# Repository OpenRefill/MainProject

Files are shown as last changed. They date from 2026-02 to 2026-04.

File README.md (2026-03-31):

# OpenRefill 
An open-source platform for refill and reuse dispenser systems. 

## The Mission
We want to accelerate the shift away from single-use plastic by enabling open, low-cost refill dispensing systems, through open-source designs, shared standards, and collaboration. Our focus is on personal care products (shampoos, conditioners, soaps, etc) that are sold to developing markets in sachets. 

Find out more at [openrefill.com](https://openrefill.com) and dive deeper at our [research wiki](https://github.com/OpenRefill/OpenRefill/wiki/Research). 

## Getting started
1. Read the [licence notice](LICENCE-NOTICE.md) and understand your freedoms and responsibilities.
2. Read our [code of conduct](CODE_OF_CONDUCT.md) and our [contribution guidelines](CONTRIBUTING.md).
3. Check out our [discussions page](https://github.com/OpenRefill/OpenRefill/discussions). Feel free to introduce yourself in [Welcome to OpenRefill Discussions!](https://github.com/OpenRefill/OpenRefill/discussions/1#discussion-9450050).
4. Review our [open issues](https://github.com/OpenRefill/MainProject/issues) to start contributing.
5. Understand the logistics, operational, and business model dimensions of deploying a refill service by heading to [Refill Realities](https://www.refillrealities.com/#playbooks) and reading their playbooks. 

## Need help? 
- Email us at hello@openrefill.com.

## Follow Us 
[LinkedIn](https://www.linkedin.com/company/open-refill/?viewAsMember=true) 
#openrefill 
#refillrevolution

## Original Contributors

OpenRefill is a collaborative effort brought to life by industry leaders in smart logistics, digital innovation, and global sustainability:

* **[Smartfill](https://smartfill.store)** – A leading global supplier of smart dispensers and cloud-based logistics and inventory management for bulk products.
* **[DY|DX Digital](https://dydx.digital)** – A leading innovation consultancy.
* **[TRANSFORM](https://www.transform.global/home.html)** – A joint initiative between Unilever, the UK Foreign, Commonwealth & Development Office (FCDO), and EY.
* **[BOPINC](https://bopinc.org)** & **[Unilever Bangladesh](https://www.unilever.com.bd/)** – Strategic partners whose work on the **URefill** project provided foundational results for this initiative.

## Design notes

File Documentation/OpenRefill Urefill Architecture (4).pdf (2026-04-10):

# OpenRefill Technical Architecture:

## Urefill Version

2026/03/03

# Overview

The U-Refill cabinet contains 4 liquid personal care dispensers. Each dispenser has the following main components:
- 1x Peristaltic pump
- 1x LCD screen
- 4x Buttons
- 1x Trigger nozzle
- 1x Loadcell
- 1x Peripheral PCB

All the components are attached to the main cabinet, which consists of laser cut and bent metal parts. Some 3d-printed parts are also used, e.g., the button covers.

The dispenser functions as follows:
1. User selects an amount
2. User presses trigger button/nozzle upwards
3. The pump runs for a calibrated time period for the selected volume
4. A receipt is printed out.
5. The dispense event is sent to the cloud interface.

The dispenser load cell weighs the dispenser hopper (5L bottle or jerry can). The loadcell reading can be used to determine if the hopper is empty. Currently though the loadcell implementation is not functional and needs to be redesigned.

### Version History

This document pertains to the U-refill project version. A minor upgrade was manually made to improve the flow rate in 2024. Also an alternative and improved hopper bracket was designed, however not implemented during this time. The main PCB was also updated to include a ground plane. Previously it only had ground traces.

# Mechanical Components

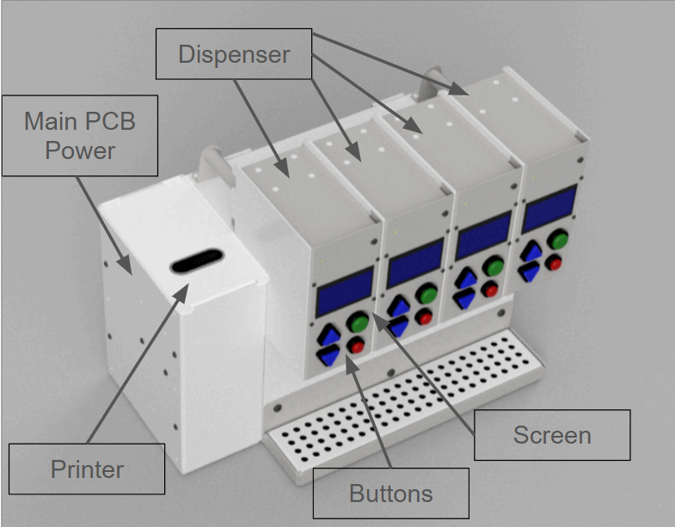
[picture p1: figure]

The cabinet has four dispensers, with a shared power supply, main PCB and printer.

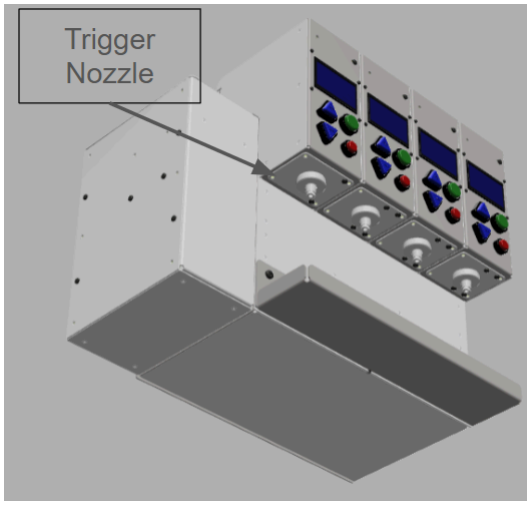
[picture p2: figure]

The trigger nozzle - this is pressed up to start dispensing after selecting an amount.

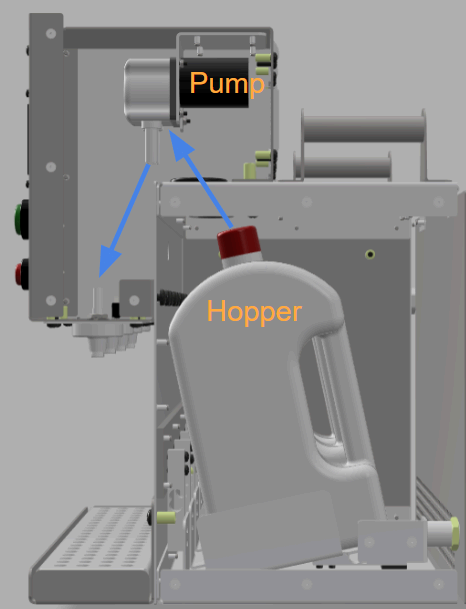
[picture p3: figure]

Side view of a dispenser. The hopper (5L jerrycan or bottle), contains the product supply. The motor pumps the liquid through the tube (blue arrows) to the Trigger Nozzle. Note this shows the updated design for the corrected load cell orientation.

# Electronics

The main PCB controls all four dispensers. The PCB has three ESP32 development boards. The boards communicate with each other using I2C.

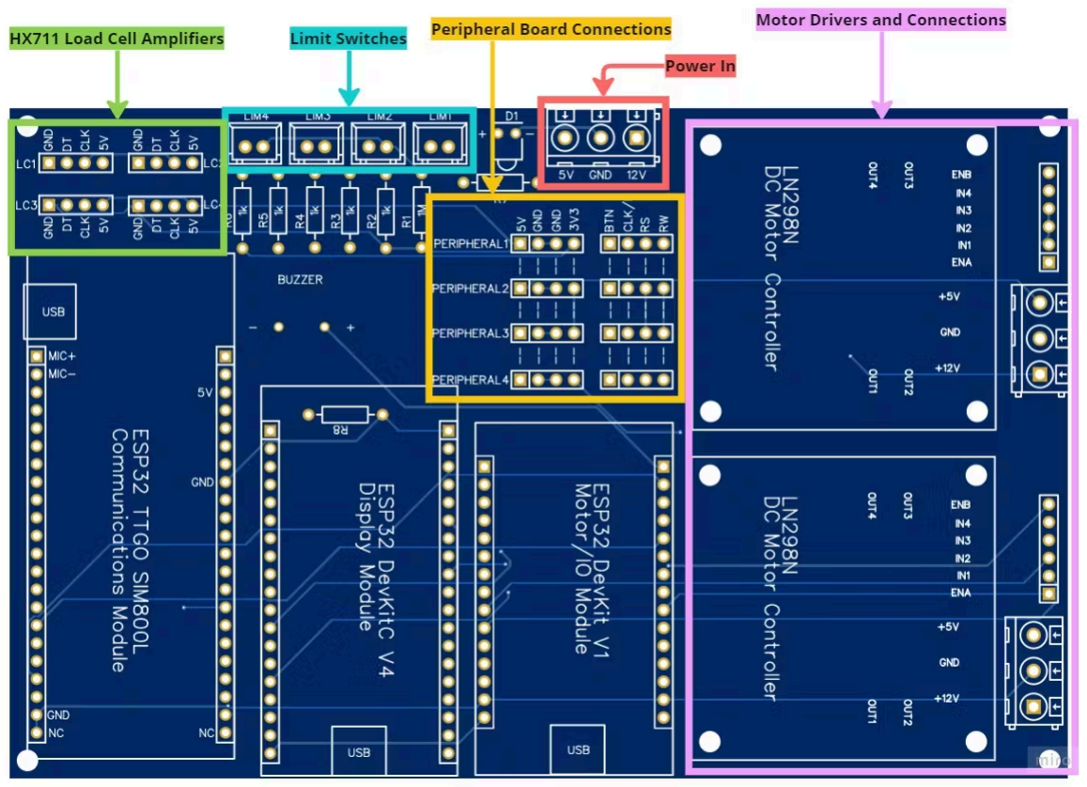
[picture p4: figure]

The main PCB with connection headers.

### Comms Module

Development Board: LILYGO TTGO T-Call V1.4 CH9102F QFN24 ESP32 Wireless Module GPRS Antenna SIM Card SIM800L Board

This ESP communicates with Azure-IoT-Central. The sim-card module mounted on it however does not work with the IoT/ESP internet library, and is not used. A WiFi router is used instead. Internet connection is used to send status updates and dispense events (records) to the cloud database. The current time is also obtained with NTP sync.

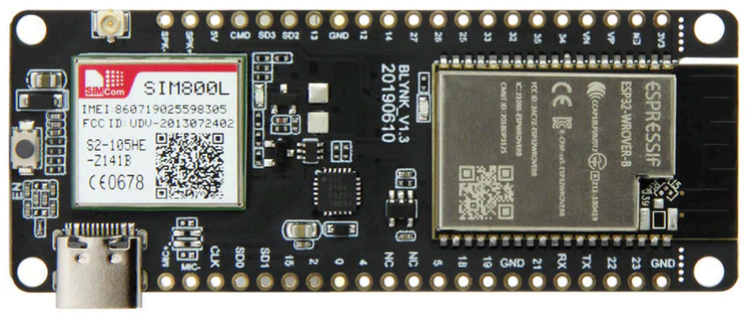
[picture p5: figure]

The LilyGo ESP module with SIM card slot

The loadcell ADC boards are also connected to this ESP. But as noted, the load cell circuit and mechanical orientation are not functional. The HX711 module (breakout board) is used to convert the load cell signal into a digital value using an ADC. The ADC digital output might need to be level shifted (5V to 3.3V).

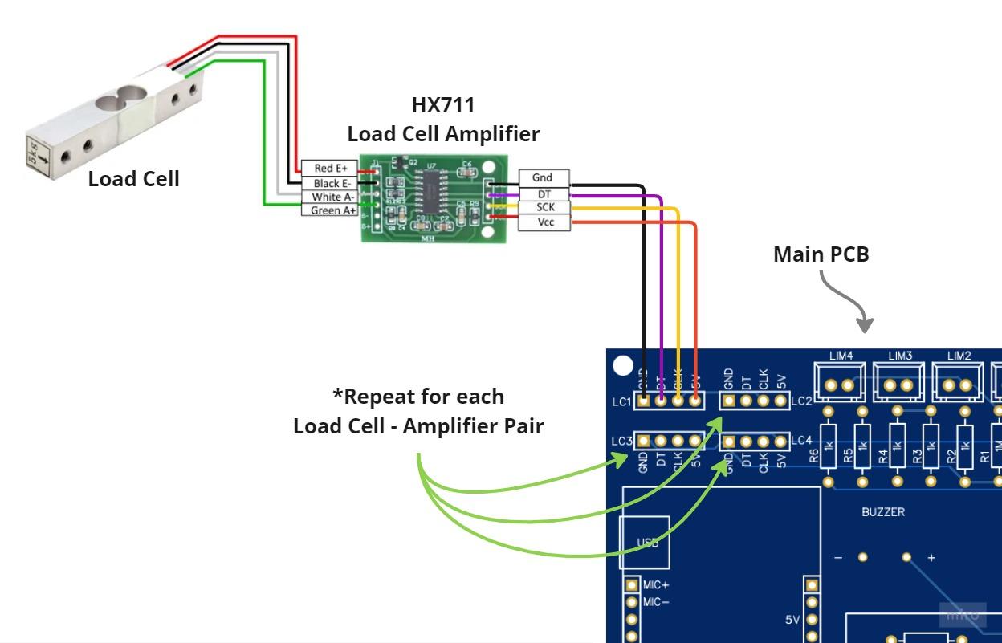
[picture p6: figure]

The loadcell connected to an HX711 loadcell ADC and amplifier, which is connected to the main PCB

### Display Module

Development Board: ESP32-WROOM32 DevKitC V4

This ESP drives all the displays. The display is a 128x64 LCD character display . Currently, the display is set to use only Bangladeshi characters.

The display module connects to each display with the Peripheral PCB.

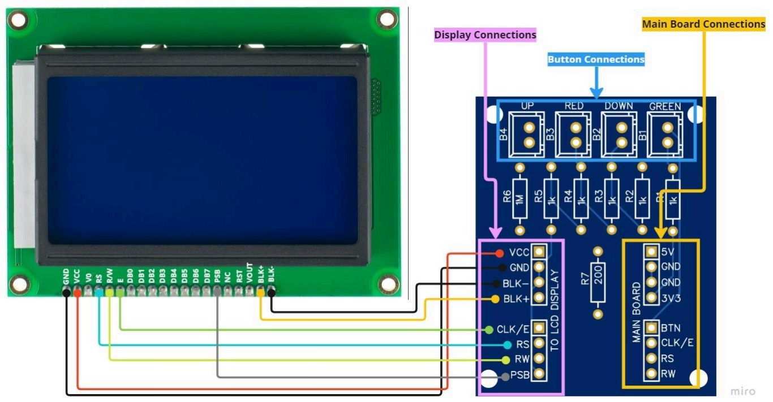
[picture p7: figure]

The display module connected to the peripheral PCB

### Main (Motor and IO) Module

Development Board: ESP32-WROOM32 DEVKIT V1

The main board does the following:
- Controls the four pump motors with DC motor drivers (also breakout boards).
- Check the buttons and trigger status of each dispenser. A resistor ladder is used to reduce the number of input pins required. All the buttons for one dispenser are connected to one pin. The voltage level as read with the ADC is used to determine if a specific button is pressed or not. The four nozzle-trigger buttons are also joined together using the same technique. The buttons are wired via the peripheral PCB to the main PCB.
- Control the buzzer.
- Connects to the Bluetooth printer to print receipts.

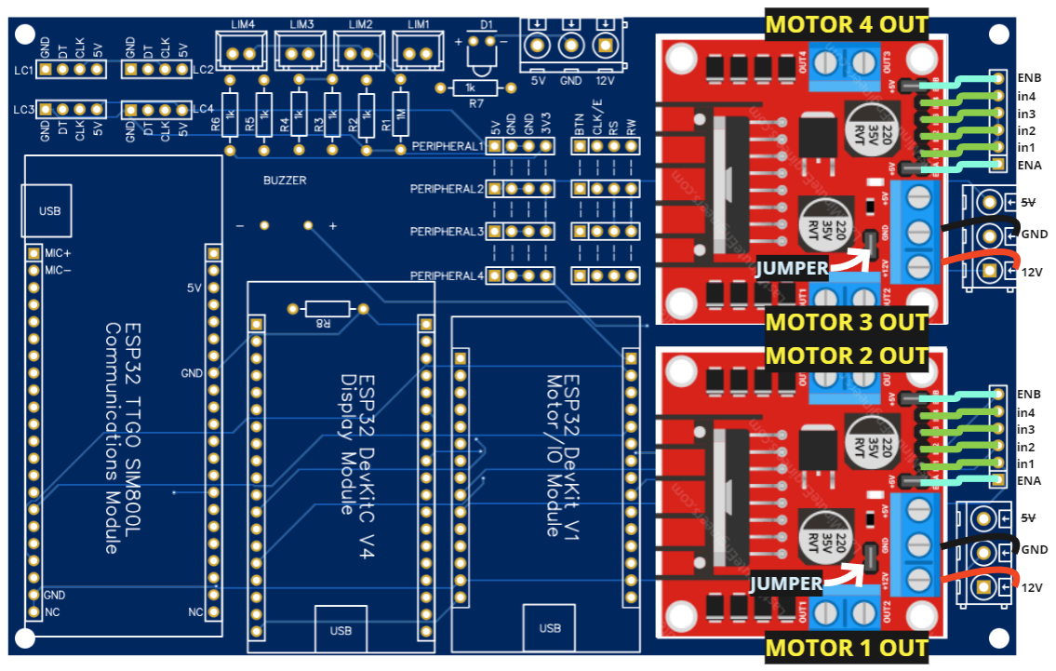
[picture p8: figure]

View of motor drivers mounted on the main PCB

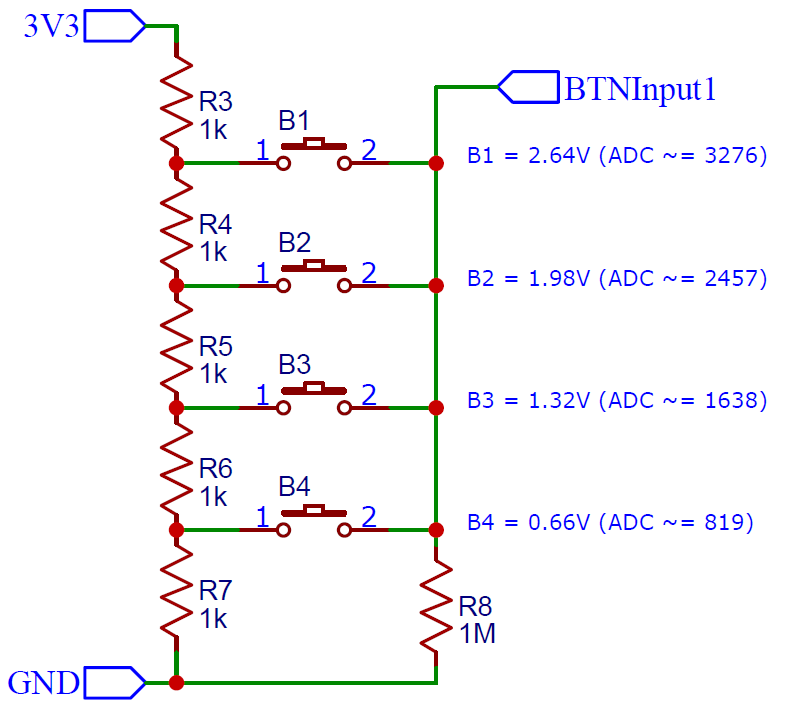
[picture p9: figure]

Voltage ladder used for buttons

### Pin Assignments: Peripheral PCB to Main Board

Pin Name | Pin Type | Description | Notes
5V | Power | 5V Power in
GND | Ground | Signal ground
3V3 | Analog Input | 3.3V reference for button circuit
BTN | Analog Output | Analog button voltage out
CLK/E | Serial Clock | Display clock
RS | Serial Data | Display chip select
R/W | Serial Data | Display data

### Pin Assignments: Peripheral to Display

Pin Name | Pin Type | Description | Notes
VCC | Power | 5V Power
GND | Ground | Signal ground
BLK- | Ground | Backlight cathode (-)
BLK+ | Power | Backlight anode (+)
CLK/E | Serial Clock | Display clock

RS | Serial Data | Display chip select
R/W | Serial Data | Display data
PSB | Digital Input | Parallel/Serial Bit (0=Serial)

## Power Supply

A 12V 10A (120W) power supply with battery connection is used to power the cabinet. A buck converter outputs the 5V power rail, which supplies the screens and ESP boards.

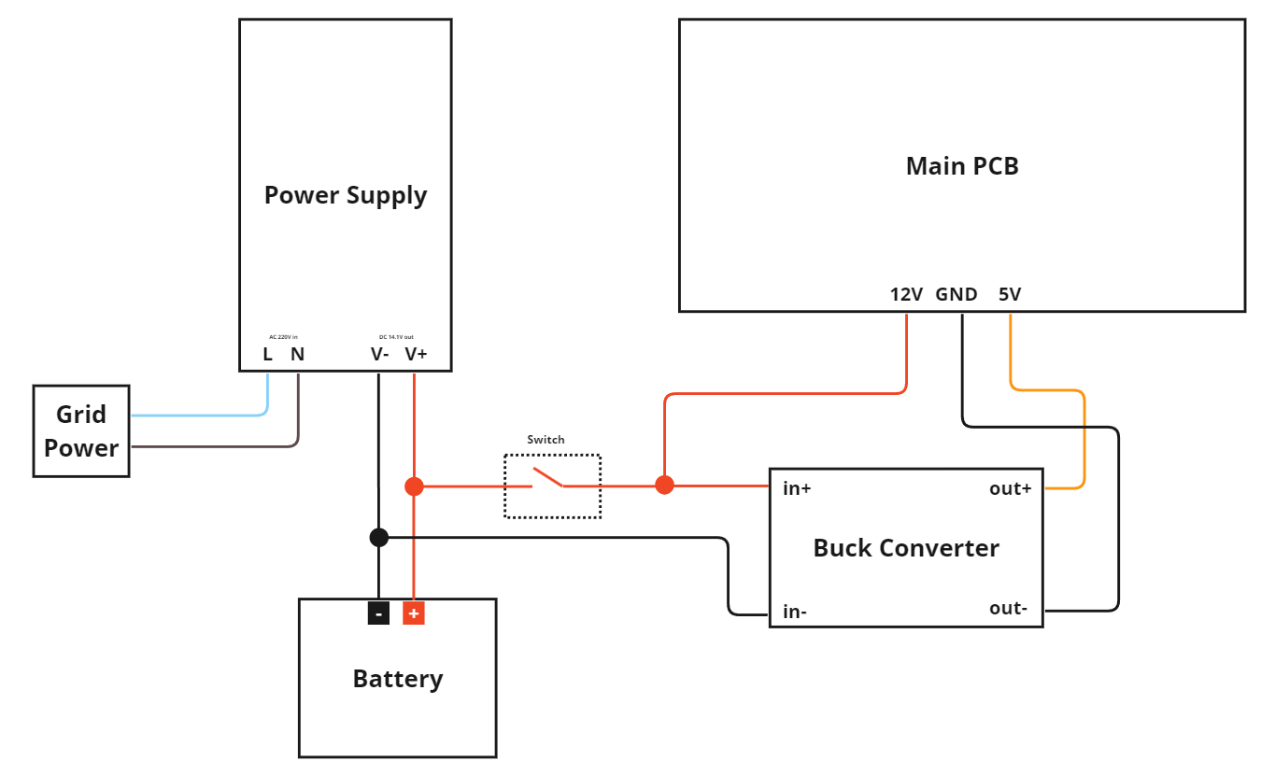
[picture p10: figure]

Block diagram of the power supply

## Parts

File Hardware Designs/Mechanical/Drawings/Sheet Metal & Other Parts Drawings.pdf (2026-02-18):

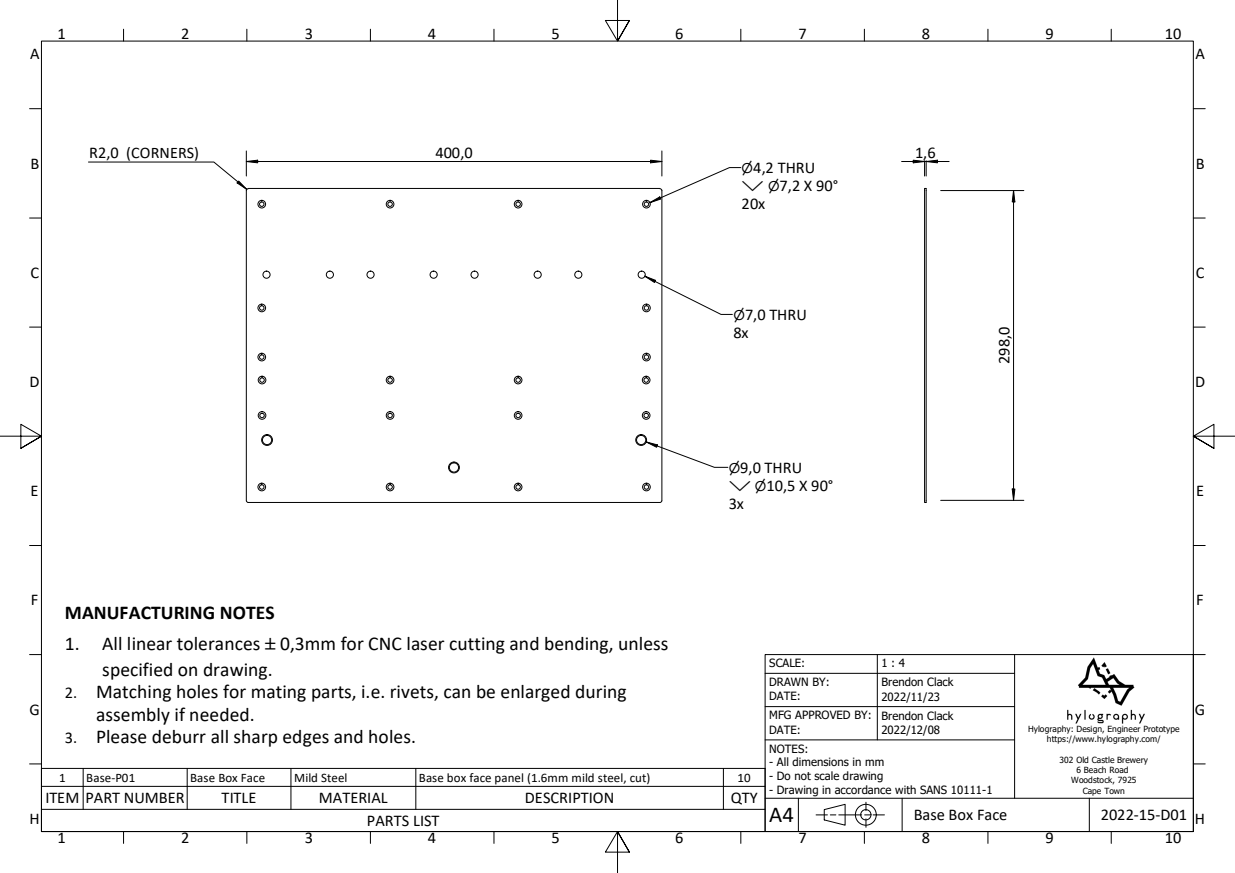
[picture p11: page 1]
PARTS LIST; Base Box Face; ⌀4,2 THRU ⌵ ⌀7,2 X 90°; ⌀7,0 THRU; ⌀9,0 THRU ⌵ ⌀10,5 X 90°; R2,0 (CORNERS)

MANUFACTURING NOTES
1. All linear tolerances `0,3mm for CNC laser cutting and bending, unless
specified on drawing.
2. Matching holes for mating parts, i.e. rivets, can be enlarged during
3. Please deburr all sharp edges and holes.

DRAWN BY: DATE: | Brendon Clack 2022/11/23

assembly if needed.

MFG APPROVED BY: DATE: | Brendon Clack 2022/12/08

Hylography: Design, Engineer Prototype
https://www.hylography.com/

NOTES:
- All dimensions in mm
- Do not scale drawing
- Drawing in accordance with SANS 10111-1

302 Old Castle Brewery
6 Beach Road
Woodstock, 7925
Cape Town

1 | Base-P01 | Base Box Face | Mild Steel | Base box face panel (1.6mm mild steel, cut) | 10
ITEM | PART NUMBER | TITLE | MATERIAL | DESCRIPTION | QTY

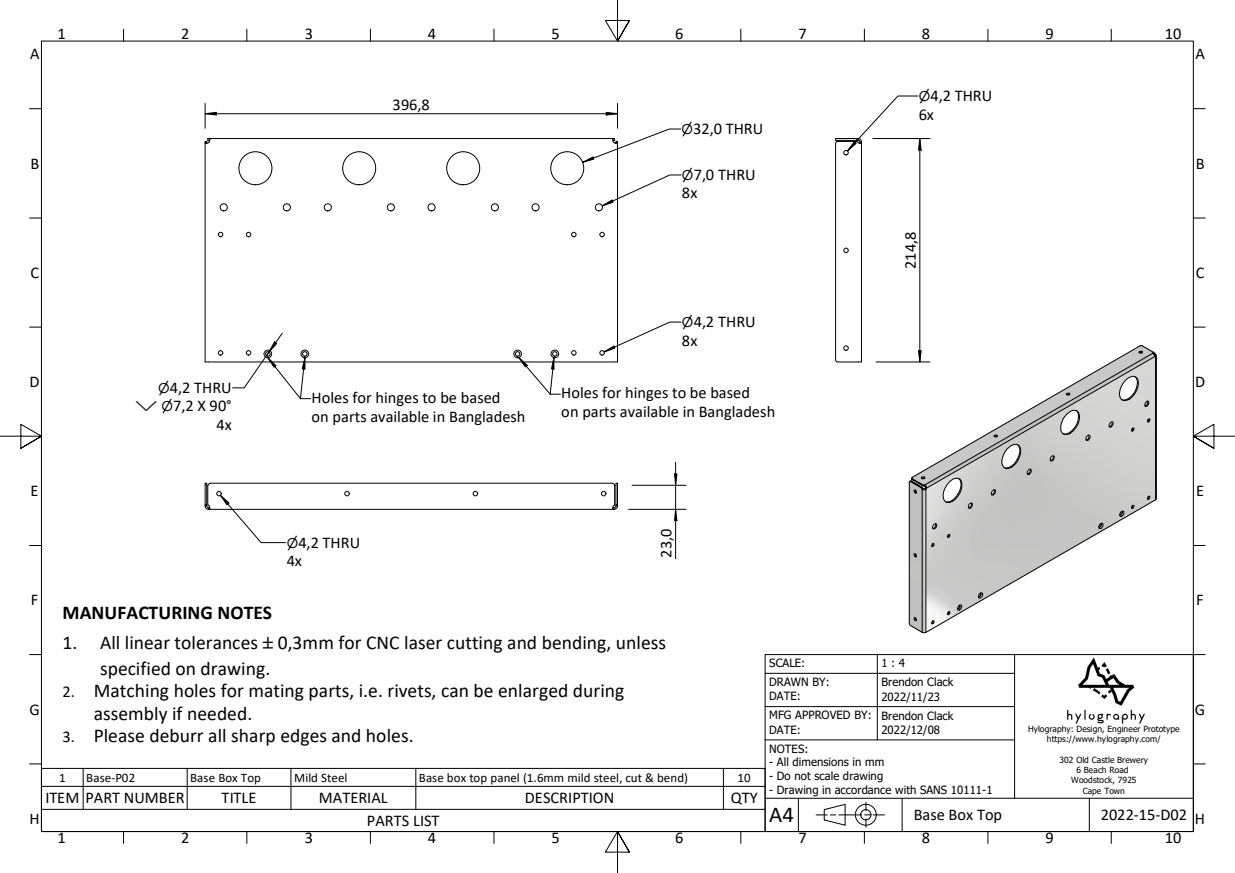
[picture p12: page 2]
Base Box Top; ⌀32,0 THRU; ⌀7,0 THRU; ⌀4,2 THRU ⌵ ⌀7,2 X 90°; ⌀4,2 THRU

Holes for hinges to be based
on parts available in Bangladesh

MANUFACTURING NOTES
1. All linear tolerances `0,3mm for CNC laser cutting and bending, unless
specified on drawing.
2. Matching holes for mating parts, i.e. rivets, can be enlarged during
3. Please deburr all sharp edges and holes.

DRAWN BY: DATE: | Brendon Clack 2022/11/23

assembly if needed.

MFG APPROVED BY: DATE: | Brendon Clack 2022/12/08

Hylography: Design, Engineer Prototype
https://www.hylography.com/

NOTES:
- All dimensions in mm
- Do not scale drawing
- Drawing in accordance with SANS 10111-1

302 Old Castle Brewery
6 Beach Road
Woodstock, 7925
Cape Town

1 | Base-P02 | Base Box Top | Mild Steel | Base box top panel (1.6mm mild steel, cut & bend) | 10
ITEM | PART NUMBER | TITLE | MATERIAL | DESCRIPTION | QTY

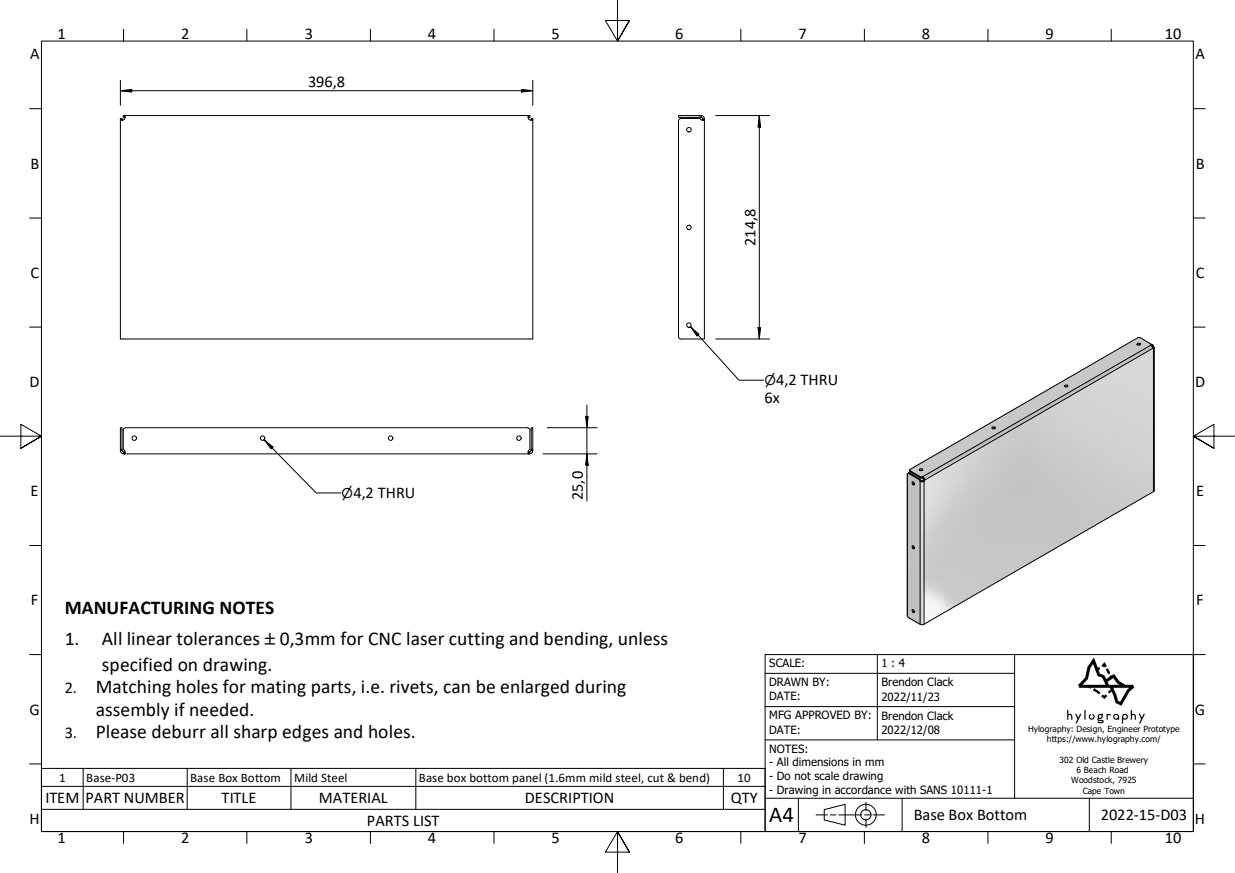
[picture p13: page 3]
Base Box Bottom; ⌀4,2 THRU

MANUFACTURING NOTES
1. All linear tolerances `0,3mm for CNC laser cutting and bending, unless
specified on drawing.
2. Matching holes for mating parts, i.e. rivets, can be enlarged during
assembly if needed.
3. Please deburr all sharp edges and holes.

DRAWN BY: DATE: | Brendon Clack 2022/11/23

MFG APPROVED BY: DATE: | Brendon Clack 2022/12/08

Hylography: Design, Engineer Prototype
https://www.hylography.com/

NOTES:
- All dimensions in mm
- Do not scale drawing
- Drawing in accordance with SANS 10111-1

302 Old Castle Brewery
6 Beach Road
Woodstock, 7925
Cape Town

1 | Base-P03 | Base Box Bottom | Mild Steel | Base box bottom panel (1.6mm mild steel, cut & bend) | 10
ITEM | PART NUMBER | TITLE | MATERIAL | DESCRIPTION | QTY

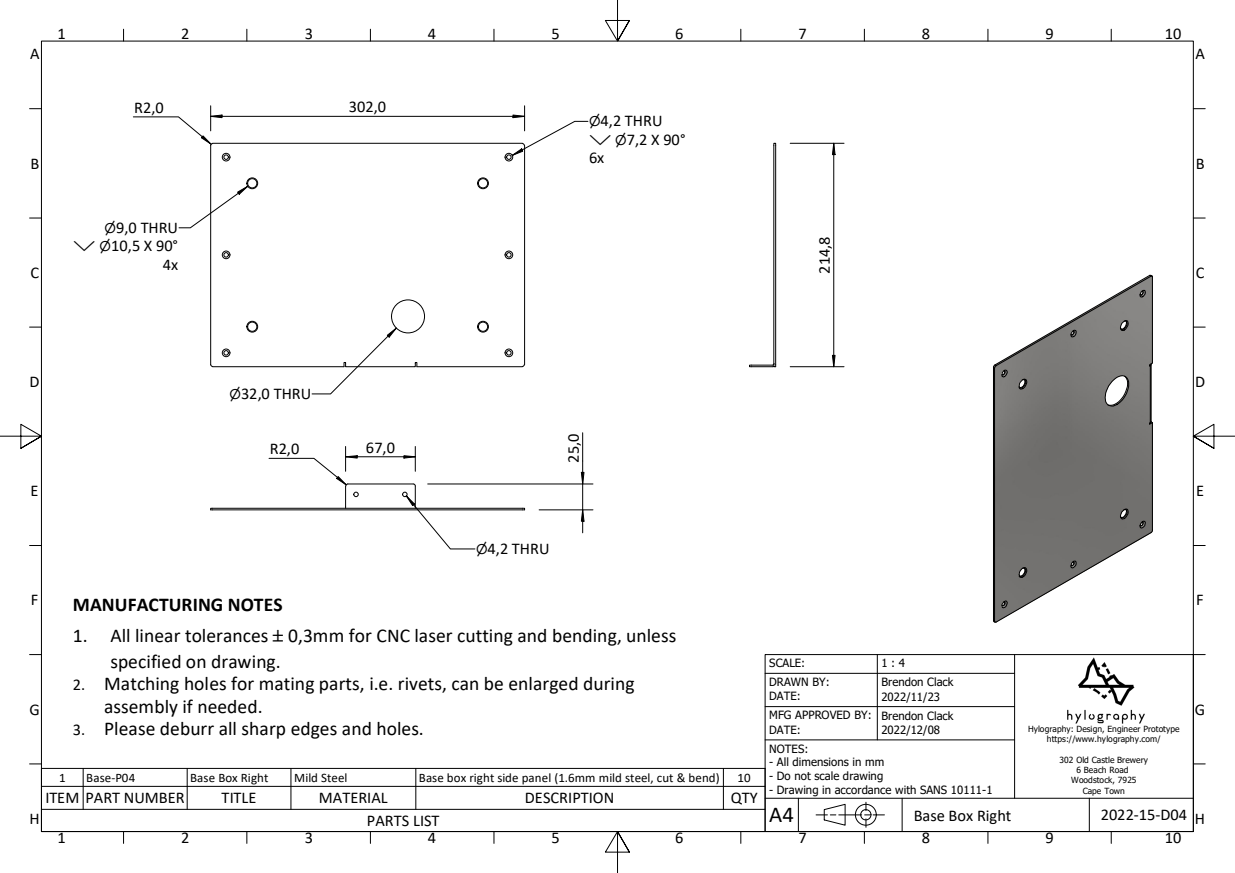
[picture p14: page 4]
Base Box Right; ⌀4,2 THRU ⌵ ⌀7,2 X 90°; ⌀32,0 THRU; ⌀4,2 THRU; ⌀9,0 THRU ⌵ ⌀10,5 X 90°

MANUFACTURING NOTES
1. All linear tolerances `0,3mm for CNC laser cutting and bending, unless
specified on drawing.
2. Matching holes for mating parts, i.e. rivets, can be enlarged during
assembly if needed.
3. Please deburr all sharp edges and holes.

DRAWN BY: DATE: | Brendon Clack 2022/11/23

MFG APPROVED BY: DATE: | Brendon Clack 2022/12/08

Hylography: Design, Engineer Prototype
https://www.hylography.com/

NOTES:
- All dimensions in mm
- Do not scale drawing
- Drawing in accordance with SANS 10111-1

302 Old Castle Brewery
6 Beach Road
Woodstock, 7925
Cape Town

1 | Base-P04 | Base Box Right | Mild Steel | Base box right side panel (1.6mm mild steel, cut & bend) | 10
ITEM | PART NUMBER | TITLE | MATERIAL | DESCRIPTION | QTY

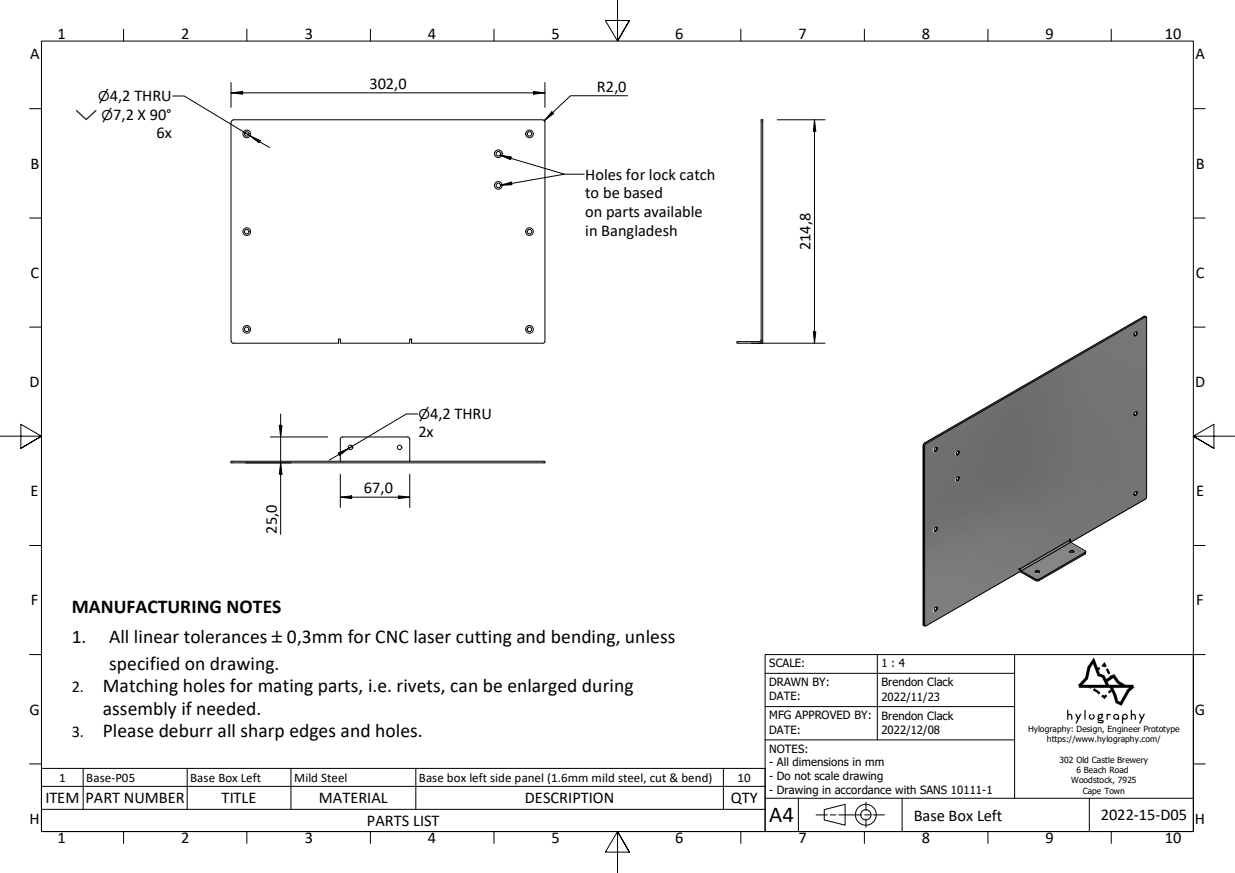
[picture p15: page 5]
Base Box Left; ⌀4,2 THRU ⌵ ⌀7,2 X 90°; ⌀4,2 THRU

Holes for lock catch
to be based
on parts available
in Bangladesh

MANUFACTURING NOTES
1. All linear tolerances `0,3mm for CNC laser cutting and bending, unless
specified on drawing.
2. Matching holes for mating parts, i.e. rivets, can be enlarged during
assembly if needed.
3. Please deburr all sharp edges and holes.

DRAWN BY: DATE: | Brendon Clack 2022/11/23

MFG APPROVED BY: DATE: | Brendon Clack 2022/12/08

Hylography: Design, Engineer Prototype
https://www.hylography.com/

NOTES:
- All dimensions in mm
- Do not scale drawing
- Drawing in accordance with SANS 10111-1

302 Old Castle Brewery
6 Beach Road
Woodstock, 7925
Cape Town

1 | Base-P05 | Base Box Left | Mild Steel | Base box left side panel (1.6mm mild steel, cut & bend) | 10
ITEM | PART NUMBER | TITLE | MATERIAL | DESCRIPTION | QTY

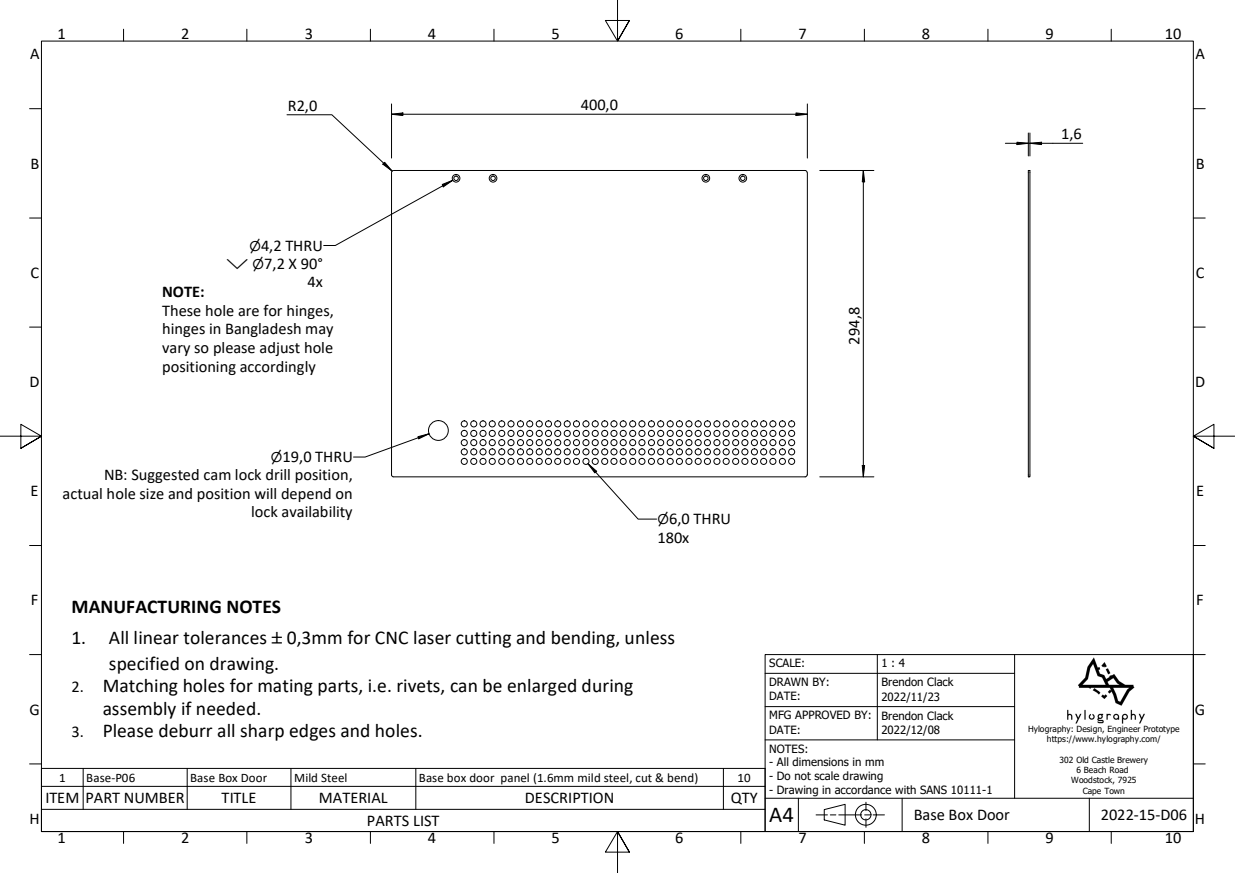
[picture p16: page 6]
Base Box Door; ⌀4,2 THRU ⌵ ⌀7,2 X 90°; ⌀6,0 THRU; ⌀19,0 THRU; lock availability

NOTE:
These hole are for hinges,
hinges in Bangladesh may
vary so please adjust hole
positioning accordingly

NB: Suggested cam lock drill position,
actual hole size and position will depend on

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

DRAWN BY: DATE: | Brendon Clack 2022/11/23

MFG APPROVED BY: DATE: | Brendon Clack 2022/12/08

Hylography: Design, Engineer Prototype
https://www.hylography.com/

NOTES:
- All dimensions in mm
- Do not scale drawing
- Drawing in accordance with SANS 10111-1

302 Old Castle Brewery
6 Beach Road
Woodstock, 7925
Cape Town

1 | Base-P06 | Base Box Door | Mild Steel | Base box door panel (1.6mm mild steel, cut & bend) | 10
ITEM | PART NUMBER | TITLE | MATERIAL | DESCRIPTION | QTY

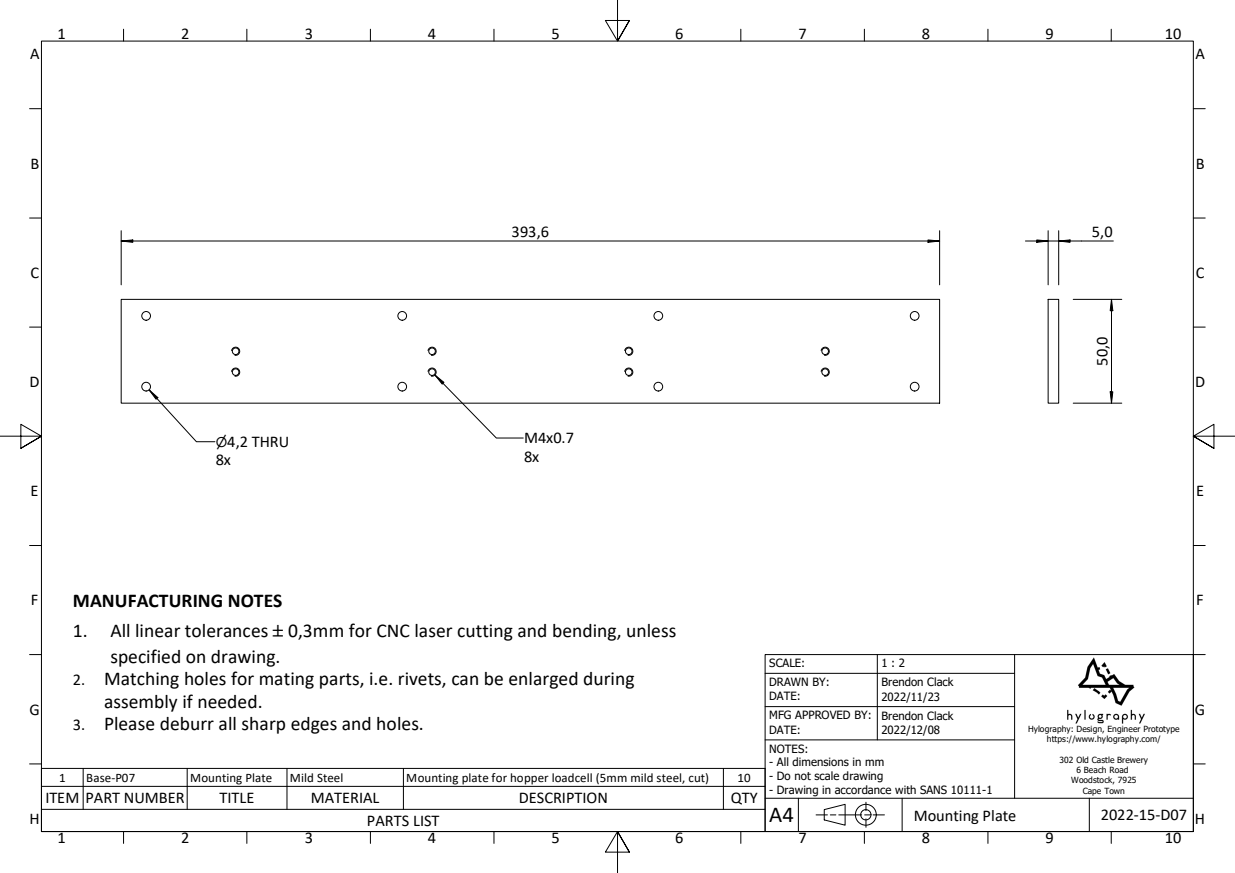
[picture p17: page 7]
Mounting Plate; ⌀4,2 THRU

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

DRAWN BY: DATE: | Brendon Clack 2022/11/23

MFG APPROVED BY: DATE: | Brendon Clack 2022/12/08

Hylography: Design, Engineer Prototype
https://www.hylography.com/

NOTES:
- All dimensions in mm
- Do not scale drawing
- Drawing in accordance with SANS 10111-1

302 Old Castle Brewery
6 Beach Road
Woodstock, 7925
Cape Town

1 | Base-P07 | Mounting Plate | Mild Steel | Mounting plate for hopper loadcell (5mm mild steel, cut) | 10
ITEM | PART NUMBER | TITLE | MATERIAL | DESCRIPTION | QTY

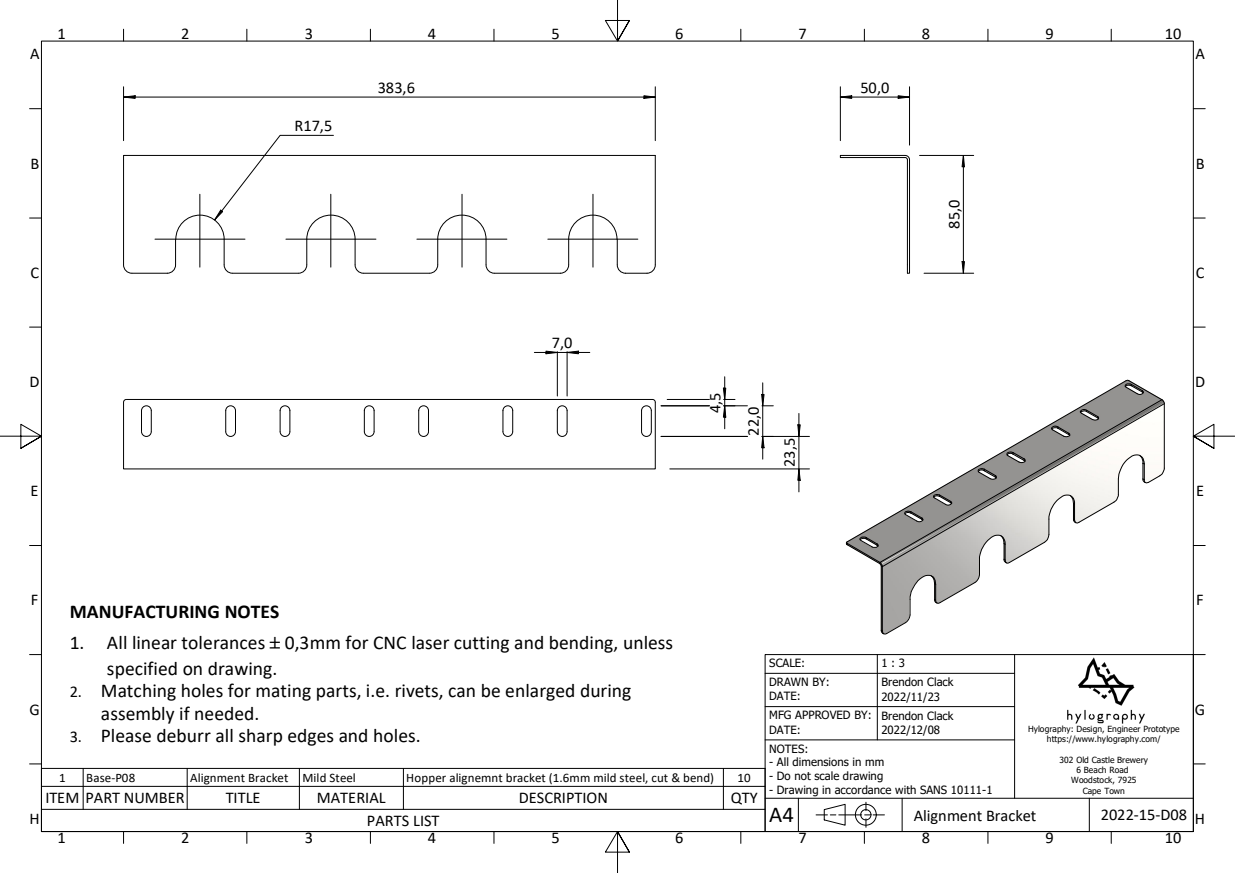
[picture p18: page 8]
Alignment Bracket

MANUFACTURING NOTES
1. All linear tolerances `0,3mm for CNC laser cutting and bending, unless
specified on drawing.
2. Matching holes for mating parts, i.e. rivets, can be enlarged during
3. Please deburr all sharp edges and holes.

DRAWN BY: DATE: | Brendon Clack 2022/11/23

assembly if needed.

MFG APPROVED BY: DATE: | Brendon Clack 2022/12/08

Hylography: Design, Engineer Prototype
https://www.hylography.com/

NOTES:
- All dimensions in mm
- Do not scale drawing
- Drawing in accordance with SANS 10111-1

302 Old Castle Brewery
6 Beach Road
Woodstock, 7925
Cape Town

1 | Base-P08 | Alignment Bracket | Mild Steel | Hopper alignemnt bracket (1.6mm mild steel, cut & bend) | 10
ITEM | PART NUMBER | TITLE | MATERIAL | DESCRIPTION | QTY

Hopper Support; ⌀5,0 THRU

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

DRAWN BY: DATE: | Brendon Clack 2022/11/23

MFG APPROVED BY: DATE: | Brendon Clack 2022/12/08

Hylography: Design, Engineer Prototype
https://www.hylography.com/

NOTES:
- All dimensions in mm
- Do not scale drawing
- Drawing in accordance with SANS 10111-1

1 | Base-P09 | Hopper Support | Mild Steel | Hopper support bracket, mounted to loadcell (2mm mild steel, cut & bend) | 40

302 Old Castle Brewery
6 Beach Road
Woodstock, 7925
Cape Town

ITEM | PART NUMBER | TITLE | MATERIAL | DESCRIPTION | QTY

Handle Bracket; ⌀19,5 THRU; ⌀4,2 THRU ⌵ ⌀ 7,2 X 90°

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

DRAWN BY: DATE: | Brendon Clack 2022/11/23

assembly if needed.

MFG APPROVED BY: DATE: | Brendon Clack 2022/12/08

Hylography: Design, Engineer Prototype
https://www.hylography.com/

NOTES:
- All dimensions in mm
- Do not scale drawing
- Drawing in accordance with SANS 10111-1

302 Old Castle Brewery
6 Beach Road
Woodstock, 7925
Cape Town

1 | Hand-P01 | Handle Bracket | Mild Steel | Base box handle bracket (1.6mm mild steel, cut & bend) | 10
ITEM | PART NUMBER | TITLE | MATERIAL | DESCRIPTION | QTY

Nozzle Mount (Pin); ⌀5,0 THRU; ⌀3,5 THRU; ⌀8,1 THRU

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

DRAWN BY: DATE: | Brendon Clack 2022/11/23

MFG APPROVED BY: DATE: | Brendon Clack 2022/12/08

Hylography: Design, Engineer Prototype
https://www.hylography.com/

NOTES:
- All dimensions in mm
- Do not scale drawing
- Drawing in accordance with SANS 10111-1

1 | Noz-P03 | Nozzle Mount (Pin) | Steel, Mild | Nozzle mounting plate assembled onto product dispensing unit (pin version) | 40

302 Old Castle Brewery
6 Beach Road
Woodstock, 7925
Cape Town

ITEM | PART NUMBER | TITLE | MATERIAL | DESCRIPTION | QTY

Switch Mount

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

DRAWN BY: DATE: | Brendon Clack 2022/11/23

assembly if needed.

MFG APPROVED BY: DATE: | Brendon Clack 2022/12/08

Hylography: Design, Engineer Prototype
https://www.hylography.com/

NOTES:
- All dimensions in mm
- Do not scale drawing
- Drawing in accordance with SANS 10111-1

302 Old Castle Brewery
6 Beach Road
Woodstock, 7925
Cape Town

1 | Noz-P04 | Switch Mount | Mild Steel | Mounting plate for limit switch | 40
ITEM | PART NUMBER | TITLE | MATERIAL | DESCRIPTION | QTY

NOTE:
These hole are for hinges,
hinges in Bangladesh may
vary so please adjust hole
positioning accordingly

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

DRAWN BY: DATE: | Brendon Clack 2022/11/23

assembly if needed.

MFG APPROVED BY: DATE: | Brendon Clack 2022/12/08

Hylography: Design, Engineer Prototype
https://www.hylography.com/

NOTES:
- All dimensions in mm
- Do not scale drawing
- Drawing in accordance with SANS 10111-1

302 Old Castle Brewery
6 Beach Road
Woodstock, 7925
Cape Town

1 | Print-P01 | Printer Box Main | Mild Steel | Printer box main enclosure (1.6mm mild steel, cut & bend) | 10
ITEM | PART NUMBER | TITLE | MATERIAL | DESCRIPTION | QTY

Printer Box Side; ⌀5,0 -1,6 DEEP

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

DRAWN BY: DATE: | Brendon Clack 2022/11/23

assembly if needed.

MFG APPROVED BY: DATE: | Brendon Clack 2022/12/08

Hylography: Design, Engineer Prototype
https://www.hylography.com/

NOTES:
- All dimensions in mm
- Do not scale drawing
- Drawing in accordance with SANS 10111-1

302 Old Castle Brewery
6 Beach Road
Woodstock, 7925
Cape Town

1 | Print-P02 | Printer Box Side | Mild Steel | Printer box removable side panel (1.6mm mild steel, cut & bend) | 10
ITEM | PART NUMBER | TITLE | MATERIAL | DESCRIPTION | QTY

Printer Box Top; ⌀4,2 THRU ⌵ ⌀ 7,2 X 90°

NOTE:
These hole are for hinges,
hinges in Bangladesh may
vary so please adjust hole
positioning accordingly

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

DRAWN BY: DATE: | Brendon Clack 2022/11/23

MFG APPROVED BY: DATE: | Brendon Clack 2022/12/08

Hylography: Design, Engineer Prototype
https://www.hylography.com/

NOTES:
- All dimensions in mm
- Do not scale drawing
- Drawing in accordance with SANS 10111-1

302 Old Castle Brewery
6 Beach Road
Woodstock, 7925
Cape Town

1 | Print-P03 | Printer Box Top | Mild Steel | Printer box hinged top lip (1.6mm mild steel, cut & bend) | 10
ITEM | PART NUMBER | TITLE | MATERIAL | DESCRIPTION | QTY

Printer Bracket; ⌀4,2 THRU

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

DRAWN BY: DATE: | Brendon Clack 2022/11/23

MFG APPROVED BY: DATE: | Brendon Clack 2022/12/08

Hylography: Design, Engineer Prototype
https://www.hylography.com/

NOTES:
- All dimensions in mm
- Do not scale drawing
- Drawing in accordance with SANS 10111-1

1 | Print-P04 | Printer Bracket | Mild Steel | Printer mounting bracket (1.6mm mild steel, cut & bend) | 10

302 Old Castle Brewery
6 Beach Road
Woodstock, 7925
Cape Town

ITEM | PART NUMBER | TITLE | MATERIAL | DESCRIPTION | QTY

Product Box Face; ⌀5,0 THRU; ⌀7,0 THRU; ⌀4,2 THRU; ⌀6,0 THRU ⌵ ⌀ 7,5 X 90°

NB: PART STILL TO BE CONFIRMED, BASED ON NEW SCREEN DIMENSIONS.

mounting to be drilled

Holes for screen

after bending,
due to proximity of
hole to bend

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

DRAWN BY: DATE: | Brendon Clack 2022/11/23

MFG APPROVED BY: DATE: | Brendon Clack 2022/12/08

Hylography: Design, Engineer Prototype
https://www.hylography.com/

NOTES:
- All dimensions in mm
- Do not scale drawing
- Drawing in accordance with SANS 10111-1

302 Old Castle Brewery
6 Beach Road
Woodstock, 7925
Cape Town

1 | Prod-P01 | Product Box Face | Mild Steel | Product box face panel (1.6mm mild steel, cut & bend) | 40
ITEM | PART NUMBER | TITLE | MATERIAL | DESCRIPTION | QTY

Product Box Cover; ⌀5,0 THRU; ⌀4,0 THRU; ⌀4,2 THRU ⌵ ⌀ 7,2 X 90°

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

DRAWN BY: DATE: | Brendon Clack 2022/11/23

MFG APPROVED BY: DATE: | Brendon Clack 2022/12/08

Hylography: Design, Engineer Prototype
https://www.hylography.com/

NOTES:
- All dimensions in mm
- Do not scale drawing
- Drawing in accordance with SANS 10111-1

1 | Prod-P02 | Product Box Cover | Mild Steel | Product box removable cover panel (1.6mm mild steel, cut & bend) | 40

302 Old Castle Brewery
6 Beach Road
Woodstock, 7925
Cape Town

ITEM | PART NUMBER | TITLE | MATERIAL | DESCRIPTION | QTY

Product Box Right; ⌀4,2 THRU ⌵ ⌀ 7,2 X 90°; ⌀6,0 THRU ⌵ ⌀ 7,5 X 90°

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

DRAWN BY: DATE: | Brendon Clack 2022/11/23

MFG APPROVED BY: DATE: | Brendon Clack 2022/12/08

Hylography: Design, Engineer Prototype
https://www.hylography.com/

NOTES:
- All dimensions in mm
- Do not scale drawing
- Drawing in accordance with SANS 10111-1

302 Old Castle Brewery
6 Beach Road
Woodstock, 7925
Cape Town

1 | Prod-P03 | Product Box Right | Mild Steel | Product right side panel (1.6mm mild steel, cut & bend) | 40
ITEM | PART NUMBER | TITLE | MATERIAL | DESCRIPTION | QTY

Product Box Left; ⌀6,0 THRU ⌵ ⌀ 7,5 X 90°; ⌀4,2 THRU ⌵ ⌀ 7,2 X 90°

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

DRAWN BY: DATE: | Brendon Clack 2022/11/23

MFG APPROVED BY: DATE: | Brendon Clack 2022/12/08

Hylography: Design, Engineer Prototype
https://www.hylography.com/

NOTES:
- All dimensions in mm
- Do not scale drawing
- Drawing in accordance with SANS 10111-1

302 Old Castle Brewery
6 Beach Road
Woodstock, 7925
Cape Town

1 | Prod-P04 | Product Box Left | Mild Steel | Product left side panel (1.6mm mild steel, cut & bend) | 40
ITEM | PART NUMBER | TITLE | MATERIAL | DESCRIPTION | QTY

pump bracket; ⌀5,0 THRU ⌵ ⌀ 6,5 X 90°; ⌀4,2 THRU

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

DRAWN BY: DATE: | Brendon Clack 2022/11/23

MFG APPROVED BY: DATE: | Brendon Clack 2022/12/08

Hylography: Design, Engineer Prototype
https://www.hylography.com/

NOTES:
- All dimensions in mm
- Do not scale drawing
- Drawing in accordance with SANS 10111-1

302 Old Castle Brewery
6 Beach Road
Woodstock, 7925
Cape Town

1 | product P03 | pump bracket | Mild Steel | Pump mounting bracket (1.6mm mild steel, cut & bend) | 40
ITEM | PART NUMBER | TITLE | MATERIAL | DESCRIPTION | QTY

Tray Support; ⌀7,0 THRU

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

DRAWN BY: DATE: | Brendon Clack 2022/11/23

MFG APPROVED BY: DATE: | Brendon Clack 2022/12/08

Hylography: Design, Engineer Prototype
https://www.hylography.com/

NOTES:
- All dimensions in mm
- Do not scale drawing
- Drawing in accordance with SANS 10111-1

1 | Tray-P01 | Tray Support | Stainless Steel AISI 304 | Drip tray support shelf (2mm mild steel, cut & bend) | 10

302 Old Castle Brewery
6 Beach Road
Woodstock, 7925
Cape Town

ITEM | PART NUMBER | TITLE | MATERIAL | DESCRIPTION | QTY

Drip Cover; ⌀10,0 THRU

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

DRAWN BY: DATE: | Brendon Clack 2022/11/23

MFG APPROVED BY: DATE: | Brendon Clack 2022/12/08

Hylography: Design, Engineer Prototype
https://www.hylography.com/

NOTES:
- All dimensions in mm
- Do not scale drawing
- Drawing in accordance with SANS 10111-1

1 | Tray-P02 | Drip Cover | Stainless Steel AISI 304 | Drip tray cover with holes (1.6mm mild steel, cut & bend) | 10

302 Old Castle Brewery
6 Beach Road
Woodstock, 7925
Cape Town

ITEM | PART NUMBER | TITLE | MATERIAL | DESCRIPTION | QTY

Handle Tube; WALL THICKNESS

MANUFACTURING NOTES
1. All linear tolerances `0,5mm.
2. Please deburr all sharp edges and holes.

DRAWN BY: DATE: | Brendon Clack 2022/11/23

MFG APPROVED BY: DATE: | Brendon Clack 2022/12/08

Hylography: Design, Engineer Prototype
https://www.hylography.com/

NOTES:
- All dimensions in mm
- Do not scale drawing
- Drawing in accordance with SANS 10111-1

302 Old Castle Brewery
6 Beach Road
Woodstock, 7925
Cape Town

1 | Hand-P02 | Handle Tube | Mild Steel | 19mm Diameter round tube (cut to 90mm length) | 20
ITEM | PART NUMBER | TITLE | MATERIAL | DESCRIPTION | QTY

Cam Lock Catch; ⌀4,2 THRU

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

DRAWN BY: DATE: | Brendon Clack 2022/11/23

MFG APPROVED BY: DATE: | Brendon Clack 2022/12/08

Hylography: Design, Engineer Prototype
https://www.hylography.com/

NOTES:
- All dimensions in mm
- Do not scale drawing
- Drawing in accordance with SANS 10111-1

302 Old Castle Brewery
6 Beach Road
Woodstock, 7925
Cape Town

1 | Base-P10 | Cam Lock Catch | Steel, Mild | Catch for engaging cam lock fro base box door | 1
ITEM | PART NUMBER | TITLE | MATERIAL | DESCRIPTION | QTY

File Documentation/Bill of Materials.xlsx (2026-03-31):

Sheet: OpenRefill BoM
Name | Use | QTY needed for 1 dispenser | Alibaba Link
500ml/Min Peristaltic pump | To dispense the product | 4 | Link (https://www.alibaba.com/product-detail/Large-Flow-Peristaltic-Pump-12V-24V_1600585318025.html)
128x64 LCD Screen | Display the UI to the customer | 4 | Link (https://www.alibaba.com/product-detail/LCD1602-module-with-IIC-I2C-Adapter_62377802918.html?s=p)
Panel Buttons | Control the UI | 16 | Link (https://www.alibaba.com/product-detail/Miniature-Momentary-Push-to-Make-Switch_60821985278.html)
3d printed button cover | Indicate button function | 16
HX711 Amp | Measure mass of products | 4 | Link (https://www.alibaba.com/product-detail/Load-Cell-1KG-5KG-10KG-20KG_1600332263212.html)
5kg Load Cell | Measure mass of products | 4
LN2988 Motor Driver | Drive the motors | 2 | Link (https://www.alibaba.com/product-detail/L298N-motor-driver-board-module-L298_62258726971.html)
ESP32 Lilyput | Communications Module | 1 | Link (https://www.alibaba.com/showroom/esp32+sim800l.html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)
ESP32 Devkit V1 | Motor/IO Module | 1 | Link (https://www.alibaba.com/product-detail/Wholesale-ESP32-ESP32S-ESP32-DEVKIT-V1_1600135879207.html)
ESP32 DevkitC V4 | Display Module | 1
Power Supply 12V 10A | Uninterrupted - power the dispenser/battery | 1
Battery | Supply 12v backup power | 1
Printer | Print receipts | 1
Limit Switches | Detect if container is under dispenser | 4
Buck cvt LM2596 |  | 1
Red jerry can caps |  | 4
White Jerry cans |  | 4
Main PCB Board (without 100uF capacitor x2 for programming) | Connect electronics | 0
100uF capacitor |  | 2
Main PCB Board (with 100uF capacitor x2 for programming) | Connect electronics | 1
Small PCB | Connect to screen/buttons | 4
Nozzle | Dispense product | 4

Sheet: URefill BoM
Thumbnail | Item | Part Number | Title | BOM Structure | Description | Material | Appearance | Vendor | QTY (1 unit) | Qty (10 units) | Status | Company
 | 1 | ASC 4x08 | Rivet Countersunk 4x8 | Purchased | Aluminium-steel countersunk rivet (4 x 8mm) Grip rage: 2-5mm | Aluminium/Steel Mandrel | As Supplied | RiVCO Products | 100 | 1000 | Pending prototype testing | Wizkit | https://github.com/OpenRefill/MainProject/blob/main/Documentation/Bill%20of%20Materials.xlsx
 | 2 | ASC 4x10 | Rivet Countersunk 4x10 | Purchased | Aluminium-steel countersunk rivet (4 x 10mm) Grip rage: 4-7mm | Aluminium/Steel Mandrel | As Supplied | RiVCO Products | 8 | 80 | Pending prototype testing | Wizkit
 | 3 | Base-P01 | Base Box Face | Normal | Base box face panel (1.6mm mild steel, cut) | Mild Steel | Powder Coated Black | Schuurman Lasercut | 1 | 10 | Pending prototype testing | Wizkit
 | 4 | Base-P02 | Base Box Top | Normal | Base box top panel (1.6mm mild steel, cut & bend) | Mild Steel | Powder Coated Black | Schuurman Lasercut | 1 | 10 | Pending prototype testing | Wizkit
 | 5 | Base-P03 | Base Box Bottom | Normal | Base box bottom panel (1.6mm mild steel, cut & bend) | Mild Steel | Powder Coated Black | Schuurman Lasercut | 1 | 10 | Pending prototype testing | Wizkit
 | 6 | Base-P04 | Base Box Right | Normal | Base box right side panel (1.6mm mild steel, cut & bend) | Mild Steel | Powder Coated Black | Schuurman Lasercut | 1 | 10 | Pending prototype testing | Wizkit
 | 7 | Base-P05 | Base Box Left | Normal | Base box left side panel (1.6mm mild steel, cut & bend) | Mild Steel | Powder Coated Black | Schuurman Lasercut | 1 | 10 | Pending prototype testing | Wizkit
 | 8 | Base-P06 | Base Box Door | Normal | Base box door panel (1.6mm mild steel, cut & bend) | Mild Steel | Powder Coated Black | Schuurman Lasercut | 1 | 10 | Pending prototype testing | Wizkit
 | 9 | Base-P07 | Mounting Plate | Normal | Mounting plate for hopper loadcell (5mm mild steel, cut) | Mild Steel | Powder Coated Black | Schuurman Lasercut | 1 | 10 | Pending prototype testing | Wizkit
 | 10 | Base-P08 | Alignment Bracket | Normal | Hopper alignemnt bracket (1.6mm mild steel, cut & bend) | Mild Steel | Powder Coated Black | Schuurman Lasercut | 1 | 10 | Pending prototype testing | Wizkit
 | 11 | Base-P09 | Hopper Support | Normal | Hopper support bracket, mounted to loadcell (2mm mild steel, cut & bend) | Mild Steel | Powder Coated Black | Schuurman Lasercut | 4 | 40 | Pending prototype testing | Wizkit
 | 12 | Butt-P01 | Small Push Button | Purchased | Small momentary push button, panel mount | Varies | As Supplied | DYDX Digital | 16 | 160 | Ready for purchasing | DYDX Digital
 | 13 | Butt-P02 | Switch Spring Washer | Purchased | Spring washer for small push button | Steel, Carbon | As Supplied | DYDX Digital | 16 | 160 | Ready for purchasing | DYDX Digital
 | 14 | Butt-P03 | Switch Nut | Purchased | Nut for small push button (M7 x 0,75mm) | Steel, Carbon | As Supplied | DYDX Digital | 16 | 160 | Ready for purchasing | DYDX Digital
 | 15 | Butt-P04 | Button Cap Go | Normal | 3D printed green cap for 'Go' button | PLA 3D printed resin | Green | Hylography | 4 | 40 | Currently being manufactured | DYDX Digital
 | 16 | Butt-P05 | Button Surround Go | Normal | 3D printed black surrounding housing for 'Go' Button | PLA 3D printed resin | Black | Hylography | 4 | 40 | Currently being manufactured | DYDX Digital
 | 17 | Butt-P06 | Button Cap Cancel | Normal | 3D printed red cap for 'Cancel' button | PLA 3D printed resin | Red | Hylography | 4 | 40 | Currently being manufactured | DYDX Digital
 | 18 | Butt-P07 | Button Surround Cancel | Normal | 3D printed black surrounding housing for 'Cancel' Button | PLA 3D printed resin | Black | Hylography | 4 | 40 | Currently being manufactured | DYDX Digital
 | 19 | Butt-P08 | Button Cap Up | Normal | 3D printed blue cap for 'Up' button | PLA 3D printed resin | Blue | Hylography | 4 | 40 | Currently being manufactured | DYDX Digital
 | 20 | Butt-P09 | Button Surround Tri | Normal | 3D printed black triangular surrounding housing for 'Up/ Down' Button | PLA 3D printed resin | Black | Hylography | 8 | 80 | Currently being manufactured | DYDX Digital
 | 21 | Butt-P10 | Button Cap Down | Normal | 3D printed blue cap for 'Down' button | PLA 3D printed resin | Blue | Hylography | 4 | 40 | Currently being manufactured | DYDX Digital
 | 22 | DP 3x10 | Dowel Pin 3x10 | Normal | Hardened and lapped dowel pin (3 x 10 mm) | Steel, Carbon | As Supplied | Topfast | 16 | 160 | All parts purchased | DYDX Digital
 | 23 | Elec-P02 | LCD Bracket | Normal | 3D printed LCD bracket and spacer to mount to front dispenser panel | PLA 3D printed resin | White | Hylography | 4 | 40 | Pending prototype testing | DYDX Digital
 | 24 | Elec-P03 | Load Cell (5kg) | Purchased | Aluminium flexure type loadcell 5kg rated | Aluminium | As Supplied | DYDX Digital | 4 | 40 | Ready for purchasing | DYDX Digital
 |  | Elec-P04 | Micro switch | Purchased | Nozzle actuator micro switch | Varies | As Supplied |  | 4 | 40 | Ready for purchasing
 | 25 | Elec-P05 (https://www.aliexpress.us/item/2251832631392379.html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) | Peristaltic Pump | Purchased | Peristaltic pump unit, with DC motor | Varies | As Supplied | DYDX Digital | 4 | 40 | Ready for purchasing | DYDX Digital
 |  | Elec-P06 | Load cell amplifier | Purchased | Amplifier module for load cell | PCB | As Supplied |  | 4 | 40 | Ready for purchasing
 |  | Elec-07 | Button PCB | Normal | Custom PCB for control buttons | PCB | As Supplied |  | 4 | 40
 |  | Elec-08 | Battery | Purchased | 12v DC Lead-acid battery | Lead-acid | As Supplied |  | 1 | 10
 |  | Elec-09 | Power supply | Purchased | 230VAC to 12VDC Power supply with battery connection | Varies | As Supplied |  | 1 | 10
 |  | Elec-10 | Motor driver | Purchased | Motor driver module | PCB | As Supplied |  | 2 | 20
 |  | Elec-11 | Thermal Printer | Purchased | Desktop thermal printer for sales slip | Varies | As Supplied |  | 1 | 10
 |  | Elec-12 | Primary Microcontroller | Purchased | Primary Microcontroller | PCB | As Supplied |  | 1 | 10
 |  | Elec-13 | Seconary Microcontroller | Purchased | Seconary Microcontroller | PCB | As Supplied |  | 1 | 10
 | 26 | Grom-P01 | Rubber Grommet | Purchased | Rubber grommet for cabling & hose protection (drill 32mm) | Rubber | Black | Rubber Products & Mouldings | 6 | 60 | Pending prototype testing | Wizkit
 | 27 | Hand-P01 | Handle Bracket | Normal | Base box handle bracket (1.6mm mild steel, cut & bend) | Mild Steel | Powder Coated Black | Schuurman Lasercut | 4 | 40 | Pending prototype testing | Wizkit
 | 28 | Hand-P02 | Handle Tube | Normal | 19mm Diameter round tube (cut to 90mm length) | Mild Steel | Powder Coated Black | Steel and Pipes for Africa | 2 | 20 | Pending prototype testing | Wizkit
 | 29 | Hinge-P01 | Generic 50mm Hinge | Inseparable | Generic 50mm mild steel hinge | Mild Steel | Powder Coated Black | TBA | 3 | 30 | Pending prototype testing | Wizkit
 | 30 | Hopper-P01 | 1L hopper | Normal | 1 Litre plastic fluid storage container | Polypropylene | As Supplied | DYDX Digital | 4 | 40 | Ready for purchasing | Wizkit
 | 31 | Fast-P01 | ISO 4035 - M8 | Purchased | Hex half nut | Steel, Carbon | Zinc Galvanized | Topfast | 4 | 40 | Pending prototype testing | Wizkit
 | 32 | Fast-P02 | ISO 7045 - M4 x 12 | Purchased | Pan head screw with type H cross recess - product grade A | Steel, Carbon | Zinc Galvanized | Topfast | 48 | 480 | Pending prototype testing | Wizkit
 | 33 | Fast-P03 | ISO 7045 - M4 x 16 | Purchased | Pan head screw with type H cross recess - product grade A | Steel, Carbon | Zinc Galvanized | Topfast | 8 | 80 | Pending prototype testing | Wizkit
 | 34 | Fast-P04 | ISO 7045 - M5 x 12 | Purchased | Pan head screw with type H cross recess - product grade A | Steel, Carbon | Zinc Galvanized | Topfast | 8 | 80 | Pending prototype testing | Wizkit
 | 35 | Fast-P05 | ISO 7045 - M6 x 16 | Purchased | Pan head screw with type H cross recess - product grade A | Steel, Carbon | Zinc Galvanized | Topfast | 23 | 230 | Pending prototype testing | Wizkit
 | 36 | Fast-P06 | ISO 7049 - ST 2,2 x 6,5 | Purchased | Cross recessed pan head tapping screws | Steel, Carbon | Zinc Galvanized | Topfast | 8 | 80 | Pending prototype testing | Wizkit
 | 37 | Fast-P07 | ISO 7091 - ST 8 | Purchased | Plain washers - Normal series - Product grade C | Steel, Carbon | Zinc Galvanized | Topfast | 4 | 40 | Pending prototype testing | Wizkit
 | 38 | Elec-P01 | LCD unit | Purchased | LCD display module | Varies | As Supplied | DYDX Digital | 4 | 40 | Ready for purchasing | DYDX Digital
 | 39 | Noz-P01 | Nozzle Body | Normal | Dispensing nozzle with smooth shank for 1/4" hose | Stainless Steel AISI 303 | Stainless Polished | Hylography | 4 | 40 | Currently being manufactured | DYDX Digital
 | 40 | Noz-P02 | Nozzle Shroud | Normal | Plastic shroud and dispenser activation cone | Acetal Resin, White | White | Hylography | 4 | 40 | Currently being manufactured | DYDX Digital
 | 41 | Noz-P03-1 | Nozzle Mount (Pin) | Normal | Nozzle mounting plate assembled onto product dispensing unit (pin version) | Mild Steel | Powder Coated Colour | Schuurman Lasercut | 4 | 40 | Pending prototype testing | Wizkit
 | 42 | Noz-P04 | Switch Mount | Normal | Mounting plate for limit switch | Mild Steel | Powder Coated Colour | Schuurman Lasercut | 4 | 40 | Pending prototype testing | Wizkit
 |  | Noz-P05 | Nozzle Spring | Purchased | Compression spring for nozzle shroud (10mm x 12 OD) | Spring Steel | As Supplied | Gellini spring & wireworks | 4 | 40 | On order
 | 43 | Print-P01 | Printer Box Main | Normal | Printer box main enclosure (1.6mm mild steel, cut & bend) | Mild Steel | Powder Coated Black | Schuurman Lasercut | 1 | 10 | Pending prototype testing | Wizkit
 | 44 | Print-P02 | Printer Box Side | Normal | Printer box removable side panel (1.6mm mild steel, cut & bend) | Mild Steel | Powder Coated Black | Schuurman Lasercut | 1 | 10 | Pending prototype testing | Wizkit
 | 45 | Print-P03 | Printer Box Top | Normal | Printer box hinged top lip (1.6mm mild steel, cut & bend) | Mild Steel | Powder Coated Black | Schuurman Lasercut | 1 | 10 | Pending prototype testing | Wizkit
 | 46 | Print-P04 | Printer Bracket | Normal | Printer mounting bracket (1.6mm mild steel, cut & bend) | Mild Steel | Powder Coated Black | Schuurman Lasercut | 1 | 10 | Pending prototype testing | Wizkit
 | 47 | Prod-P01 | Product Box Face | Normal | Product box face panel (1.6mm mild steel, cut & bend) | Mild Steel | Powder Coated Colour | Schuurman Lasercut | 4 | 40 | Pending prototype testing | Wizkit
 | 48 | Prod-P02 | Product Box Cover | Normal | Product box removable cover panel (1.6mm mild steel, cut & bend) | Mild Steel | Powder Coated Colour | Schuurman Lasercut | 4 | 40 | Pending prototype testing | Wizkit
 | 49 | Prod-P03 | Product Box Right | Normal | Product right side panel (1.6mm mild steel, cut & bend) | Mild Steel | Powder Coated Colour | Schuurman Lasercut | 4 | 40 | Pending prototype testing | Wizkit
 | 50 | Prod-P04 | Product Box Left | Normal | Product left side panel (1.6mm mild steel, cut & bend) | Mild Steel | Powder Coated Colour | Schuurman Lasercut | 4 | 40 | Pending prototype testing | Wizkit
 | 51 | Prod-P05 | Pump Bracket | Normal | Pump mounting bracket (1.6mm mild steel, cut & bend) | Mild Steel | Powder Coated Colour | Schuurman Lasercut | 4 | 40 | Pending prototype testing | Wizkit
 | 52 | RIV-CSK M4 | M4 countersunk rivnut | Purchased | Countersunk rivnut 4mm (drill 6mm & countersunk 7,5mm) | Mild Steel | Zinc Chromate | RiVCO Products | 48 | 480 | Pending prototype testing | Wizkit
 | 53 | RIV-CSK M6 | M6 Countersunk Rivnut | Purchased | Countersunk rivnut 4mm (drill 9mm & countersunk 10,5mm) | Mild Steel | Zinc Chromate | RiVCO Products | 23 | 230 | Pending prototype testing | Wizkit
 | 54 | Tray-P01 | Tray Support | Normal | Drip tray support shelf (2mm mild steel, cut & bend) | Stainless Steel AISI 304 | Stainless Brushed | Schuurman Lasercut | 1 | 10 | Pending prototype testing | Wizkit
 | 55 | Tray-P02 | Drip Cover | Normal | Drip tray cover with holes (1.6mm mild steel, cut & bend) | Stainless Steel AISI 304 | Stainless Brushed | Schuurman Lasercut | 1 | 10 | Pending prototype testing | Wizkit
 | 56 | Tray-P03 | Drip Container | Normal | Drip collection container (1.5mm thermoformed) | ABS Plastic | Black | Polytech Thermoforming | 1 | 10 | Currently being manufactured | DYDX Digital
 | 57 | Lock-P01 | Panel Lock | Purchased | Panel lock for base box flip door | Steel, Carbon | As Supplied | TBA | 1 | 10 | Pending prototype testing | Wizkit
 | 58 | Hose-P01 | Fluid Hose | Purchased | Silicone hose for fluid delivery (9mm OD x 6mm ID) | Silicone | As Supplied | TBA | 3 | 30 | Pending prototype testing | Wizkit

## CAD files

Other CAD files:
Hardware Designs/Mechanical/Sheetmetal/C6 Base box door.dwg
Hardware Designs/Mechanical/Sheetmetal/C9 base box bottom.dwg
Hardware Designs/Mechanical/Sheetmetal/C8 base box top.dwg
Hardware Designs/Mechanical/Sheetmetal/B2v2 Printer bracket v2.dwg
Hardware Designs/Mechanical/Sheetmetal/A1 Tray support.dwg
Hardware Designs/Mechanical/Sheetmetal/A2 Drip cover tray.dwg
Hardware Designs/Mechanical/Sheetmetal/C10 base box side-left.dwg
Hardware Designs/Mechanical/Sheetmetal/B4 Printer box top cover.dwg
Hardware Designs/Mechanical/Sheetmetal/C7 base box face.dwg
Hardware Designs/Mechanical/Sheetmetal/D2v2 Product enclosure - cover v2.dwg
Hardware Designs/Mechanical/Sheetmetal/C4v2 Hopper alignment bracket v2.dwg
Hardware Designs/Mechanical/Sheetmetal/B3v2 Printer box - side panel v2.dwg
Hardware Designs/Mechanical/Sheetmetal/C2 Hopper bracket.dwg
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

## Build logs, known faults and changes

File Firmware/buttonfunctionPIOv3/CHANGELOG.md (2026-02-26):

# Todo
### Minor
- ...

### Major
- printer error:
    - [E][BLEClient.cpp:238] gattClientEventHandler(): Failed to connect, status=Unknown ESP_ERR error
    - Connected to server
    - (hangs)

### Future Features
- connect only with BLE printer with specific address

### Future Design Changes
- non-BLE printer
- flow-rate sensor or piston pump with stepper
- pump change
- pi-zero base controller instead of comms esp
- io-expander with single esp to control displays and motors

### Outstanding Tests
- pause/continue accuracy
- printer working
- test STATE_CANCEL_IN_DX

## [3.4.0] - 2024-10-15 - Fix report from TK to ML 
### Changed
- statemachine: change _selected_amount_tk --> _selected_amount_ml in "dxi2c.comsOnFinished..."
- printer: 

### Added:
- buttons: add printStreamFiltered -- prints filtered stream for testing purposes.

## [3.3.1] - 2024-09-18
### Changed:
- ESC printer -- small changes

### Added
- (disabled) MutliButtons: AEWMA filter (roll-off could cause false trigger, needs futher work)

## [3.3.0] - 2024-07-05
### Changed
- small clean up

### Added
- device lock feature
- serial: add get string vals if certain command
- device id

## [3.2.1] - 2024-07-05
### Changed
- state machine: add state STATE_CANCEL_IN_DX

## [3.2.0] - 2024-07-05
### Changed
- set voltage cmd parse: fix bug, was sending dx_num,dx_num,low, instead of dx_num, low, high

## [3.1.1] - 2024-07-02
### Changed
- receipt: changed ingredients, product category, add header Urefill and drop "you saved"

# Changelog
## [3.1.0] - 2024-06-26 - Change Log Start
### Changed
- moved thermal printer import to local src folder to remove import issue

### Removed
- config ini: escprinterble dependency 
- config-main: OPT buzzer and printer, changed to NVM config vars

### Added
- statemachine: display update timer object
- statemachine: cfg has printer and buzzer

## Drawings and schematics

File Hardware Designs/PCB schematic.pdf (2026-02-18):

## Supply (12V-15V 10A) Battery Current Regulator

## 5V Rail

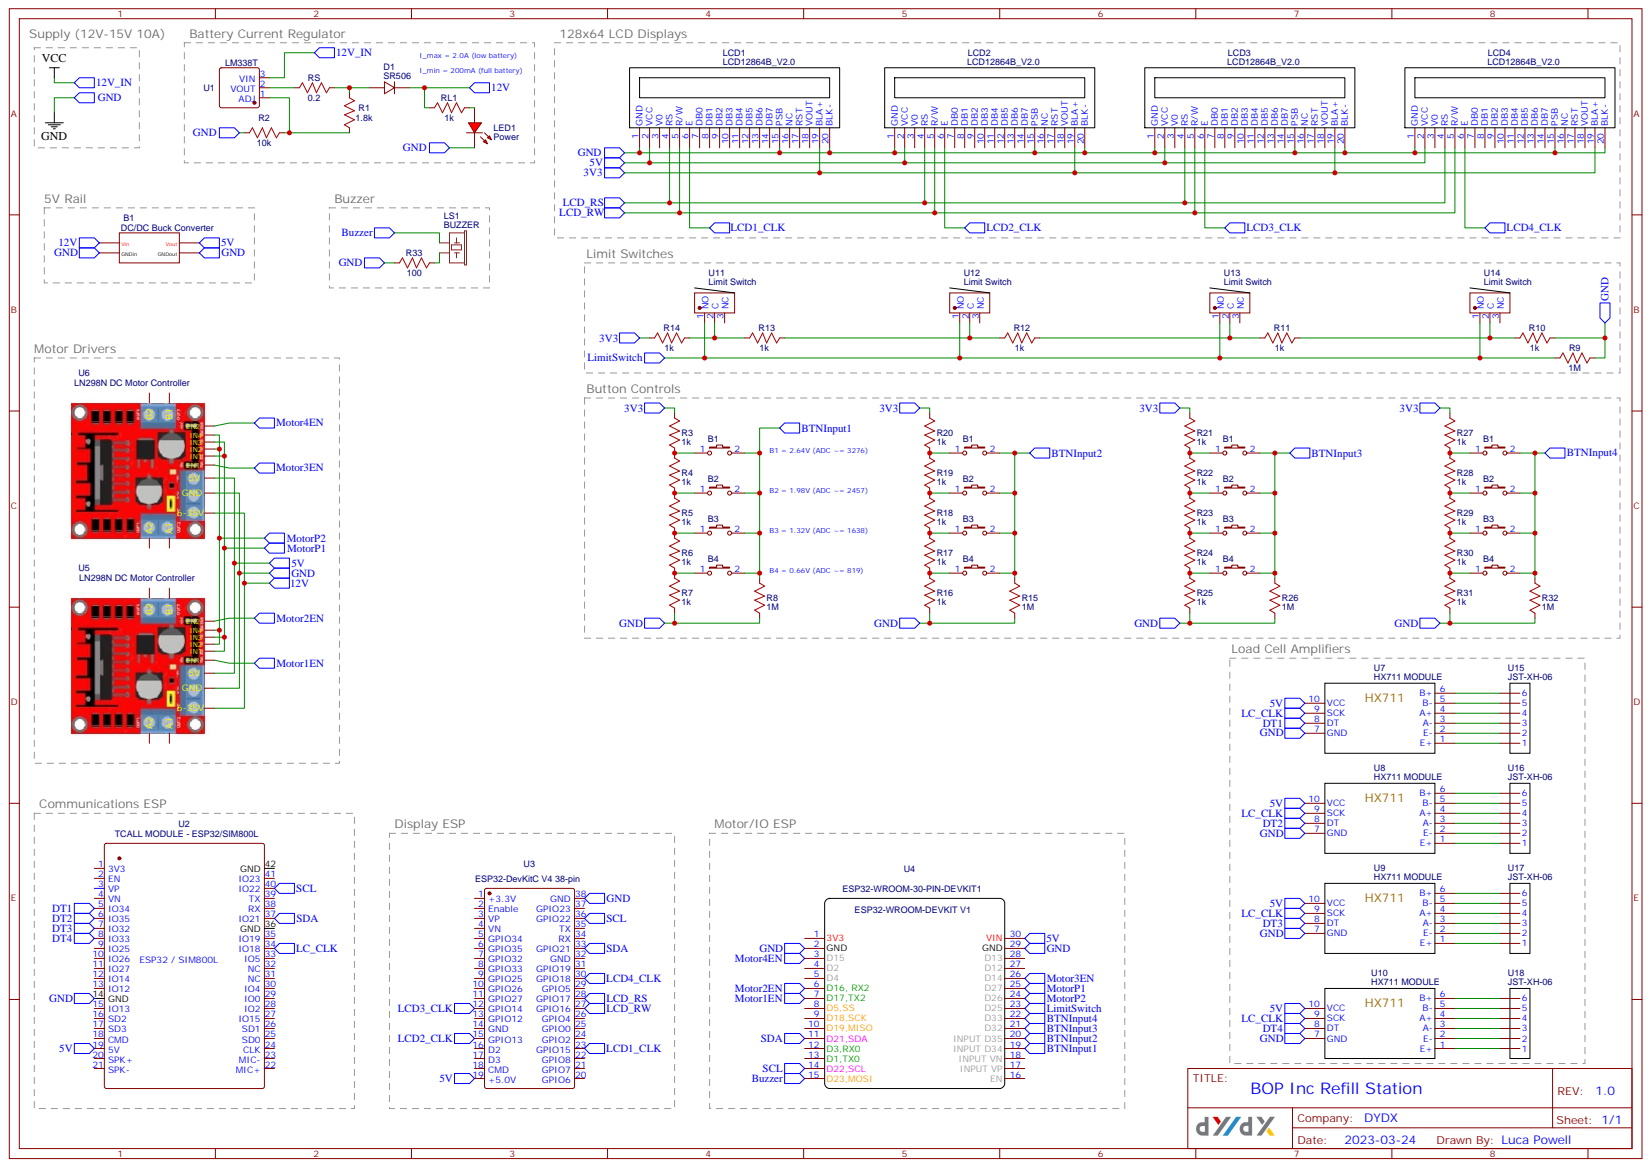
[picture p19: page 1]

DC/DC Buck Converter

Drawn By: Luca Powell

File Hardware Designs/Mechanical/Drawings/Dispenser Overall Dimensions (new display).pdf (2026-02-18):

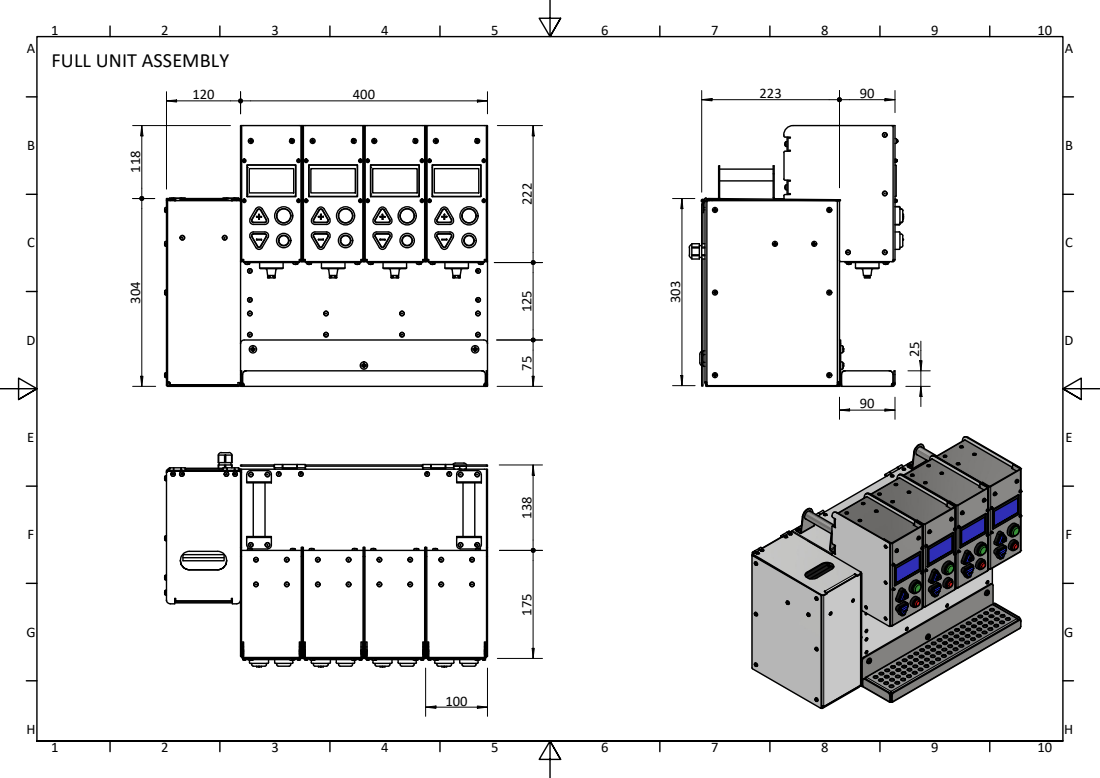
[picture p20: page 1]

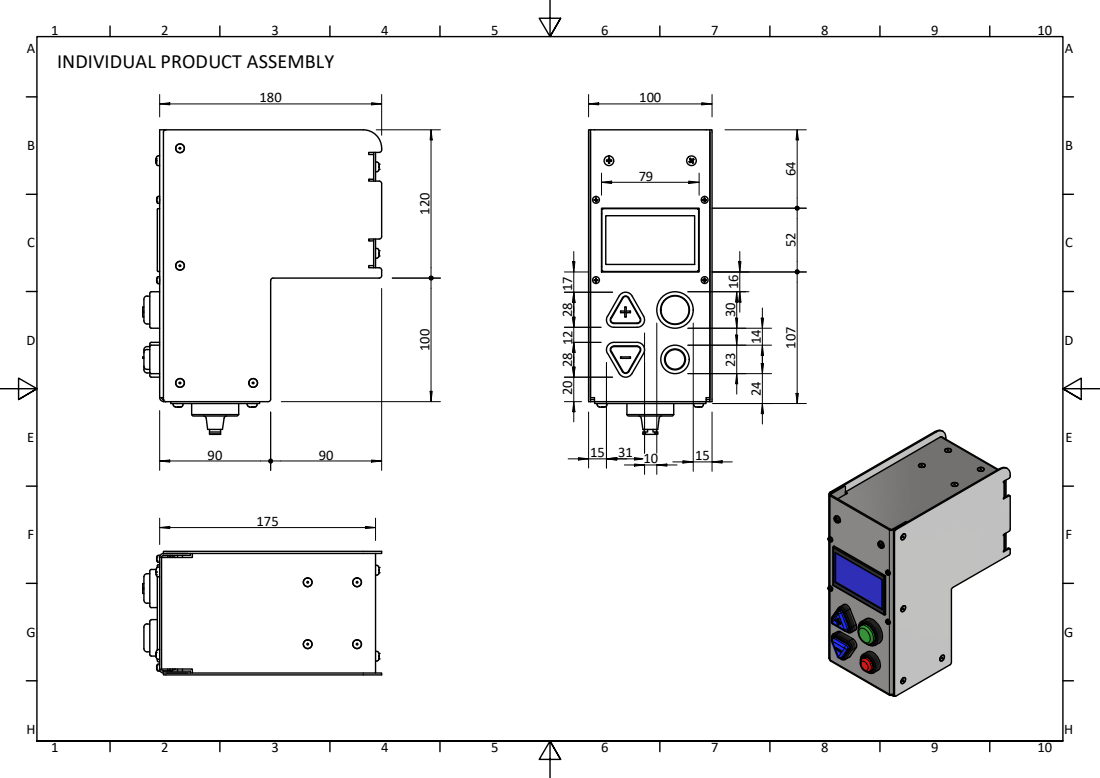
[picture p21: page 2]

INDIVIDUAL PRODUCT ASSEMBLY

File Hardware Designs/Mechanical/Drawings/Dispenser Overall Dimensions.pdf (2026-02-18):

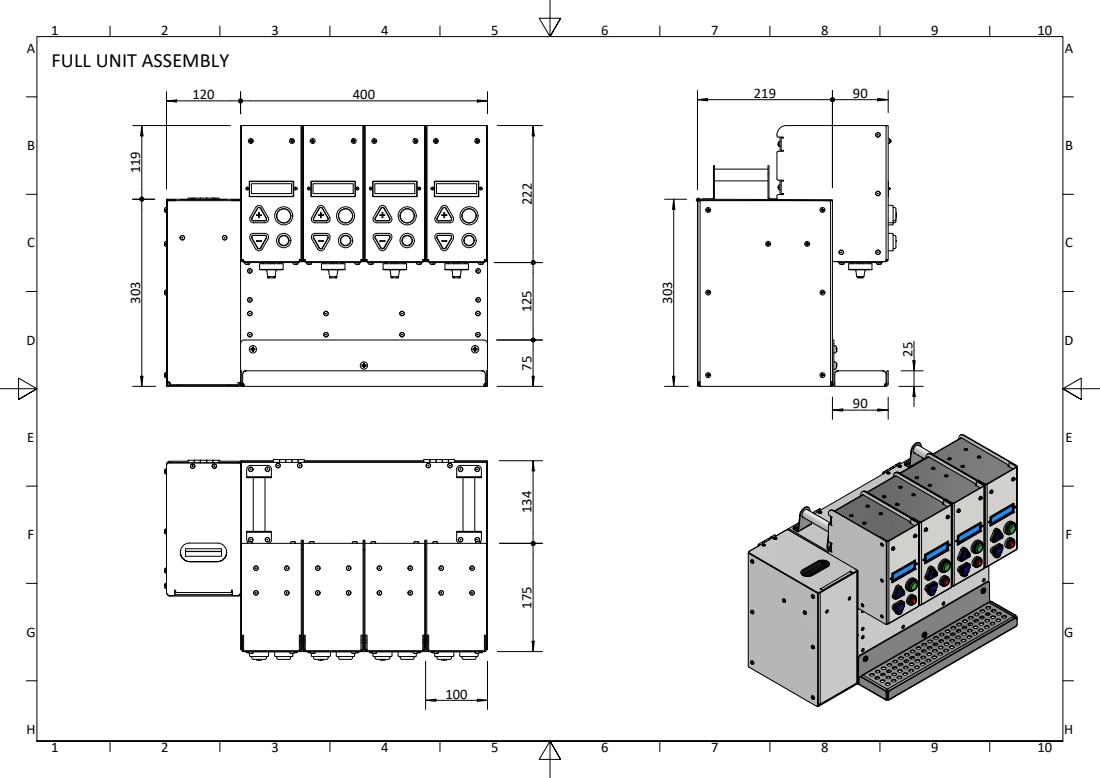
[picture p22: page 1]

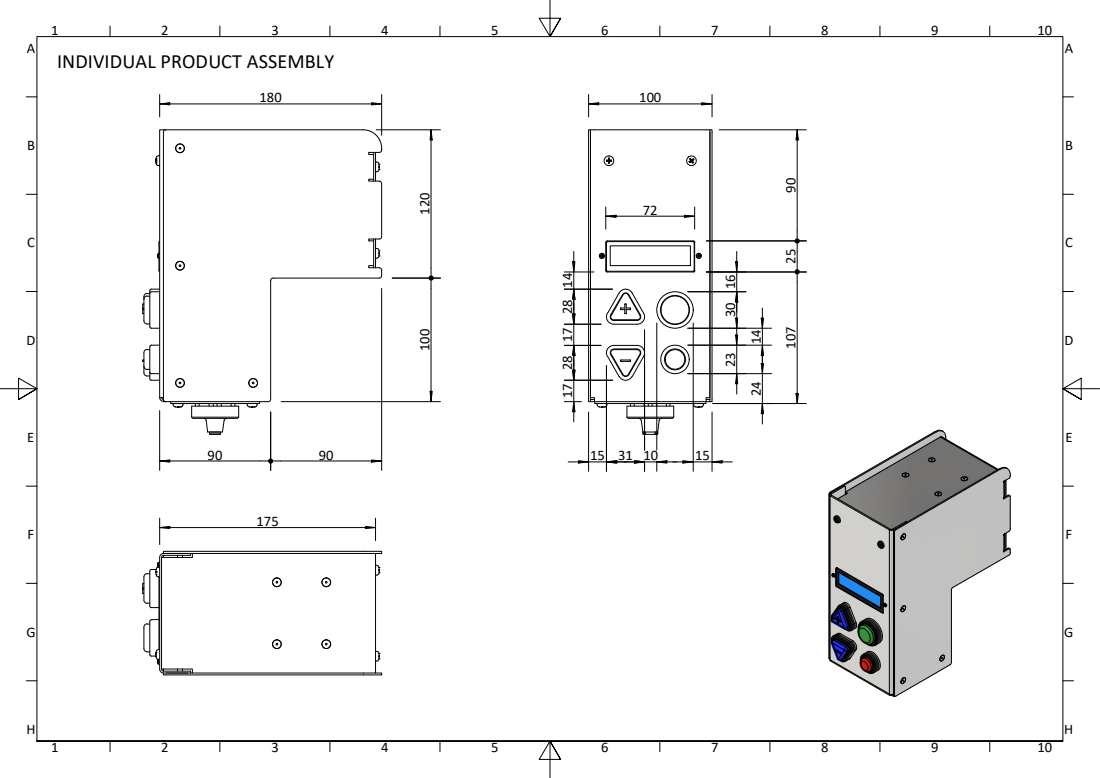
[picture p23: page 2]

INDIVIDUAL PRODUCT ASSEMBLY

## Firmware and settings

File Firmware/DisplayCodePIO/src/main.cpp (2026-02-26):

#include <Arduino.h>
#include <U8g2lib.h>
#include <SPI.h>
#include <Wire.h>

#include "dxconfigmain.h"
#include "dxchars.h"

#define I2C_DEV_ADDR 0x56

uint8_t draw_state = 0;
int activeDispenser = 0; //1 to 4
uint8_t display_current_number = 0; //0 to 3

U8G2_ST7920_128X64_F_SW_SPI display1(U8G2_R0, /* clock=*/15 /* A4 */, /* data=*/16 /* A2 */, /* CS=*/17 /* A3 */, /* reset=*/U8X8_PIN_NONE);
U8G2_ST7920_128X64_F_SW_SPI display2(U8G2_R0, /* clock=*/13 /* A4 */, /* data=*/16 /* A2 */, /* CS=*/17 /* A3 */, /* reset=*/U8X8_PIN_NONE);
U8G2_ST7920_128X64_F_SW_SPI display3(U8G2_R0, /* clock=*/14 /* A4 */, /* data=*/16 /* A2 */, /* CS=*/17 /* A3 */, /* reset=*/U8X8_PIN_NONE);
U8G2_ST7920_128X64_F_SW_SPI display4(U8G2_R0, /* clock=*/18 /* A4 */ ,/* data=*/16 /* A2 */, /* CS=*/17 /* A3 */, /* reset=*/U8X8_PIN_NONE);



U8G2_ST7920_128X64_F_SW_SPI *dispArray[NUM_DISPLAYS] = {&display1,&display2,&display3,&display4};
U8G2_ST7920_128X64_F_SW_SPI *dispCurrent = dispArray[0];

void onRequest() // Anwsers to Master's "requestFrom"
{
   // SerialMon.println("Request received. Sending buffered data."); //The sending happens on the background
}

void onReceive(int len) // Anwsers to Master's "transmissions"
{
   // The way msg have been contstructed is DispenserIndex:MSG:QTY
   String requestResponse = ""; // to generate the request reply content
   String msg_str = "";   // to save Master's message

   // char msg_char[len];
   // int msgIndex = 0;
   while (Wire.available()) // If there are bytes through I2C
   {
      msg_str.concat((char)Wire.read()); // make a string out of the bytes
   }

   // msg_str.toCharArray(msg_char, len+1);
   
   Serial.print("Master Message: ");
   Serial.println(msg_str);

   // Serial.print("First char of Master Message: ");
   // Serial.println(msg_char[0]);
   
   // if (masterMessage == "1" || masterMessage == "2" || masterMessage == "3" || masterMessage == "4") 
   if (msg_str.length() == 1 && msg_str >= "1" && msg_str <= "4") 
   {
               uint8_t disp_number = msg_str[0] - '0';  // Convert the string to uint8_t
               setActiveDisplay(disp_number);
   }
   //S:XX (send the savings value for the savings screen)
   else if (msg_str[0] == 'S')                      showYouSaved(msg_str); 
   //N:XX:XXX: (number changes on UI menu, selecting amount. Order is N:<price>:<volume>:)
   else if (msg_str[0] == 'N')                      showChangedSelection(msg_str); 
   //D:XX:XX: (dispensing progress updates. Order is D:<currentAmount>:<totalAmount>:)
   else if (msg_str[0] == 'D')                      showProgress(msg_str);
   //show text values
   else if (msg_str == "Press Green")     showPressGreen();
   else if (msg_str == "Push Bottle")     showPushBottle();
   else if (msg_str == "Cancel")          showCancel();
   else if (msg_str == "Printing")        showPrinting();
   else if (msg_str == "Finished")        showFinished();
}

void resetDisplays()
{
   for (size_t i = 0; i < NUM_DISPLAYS; i++)
   {
      resetDisplayX(i);
   }
}

void resetDisplayX(uint8_t display_number)
{
   dispArray[display_number]->clearBuffer();
   dispArray[display_number]->drawXBMP(0, 0, PushBottle_width, PushBottle_height, PushAnyBtn);
   dispArray[display_number]->sendBuffer();
}

//dx_number is from 1,2,3,4, while display number 0..3
void setActiveDisplay(uint8_t dx_number)
{
   if (dx_number <= 0 || dx_number > NUM_DISPLAYS){
      Serial.printf("set-active: error display number: %d\n",dx_number);
   }
   else{
      Serial.printf("set-active: Init %d\n",dx_number);
      activeDispenser = dx_number;
      display_current_number = dx_number-1;
      dispCurrent = dispArray[display_current_number];
      dispCurrent->begin();
      dispCurrent->clearBuffer();
      dispCurrent->drawXBMP(0, 0, takka_colon_width, takka_colon_height, takkaColon);
      dispCurrent->drawXBMP(0,32,ML_width, ML_height, ML);
      dispCurrent->sendBuffer();
   }
}

void showYouSaved(String msg)
{
   // S:XX
   uint8_t first_num, second_num, third_num;
   uint8_t num_found = getDigitsFromString(msg,2,2,first_num,second_num,third_num);

   dispCurrent->clearBuffer();
   dispCurrent->drawXBMP(0, 0, YouSaved_width, YouSaved_height, YouSaved);
   
   if (num_found == 2)
   {
      dispCurrent->drawXBMP(0, YouSaved_height, NumerialWidth, NumerialHeight, numerials_32[first_num]);
      dispCurrent->drawXBMP(NumerialWidth, YouSaved_height, NumerialWidth, NumerialHeight, numerials_32[second_num]);
   }         
   else if (num_found == 1)
   {
      dispCurrent->drawXBMP(NumerialWidth, YouSaved_height, NumerialWidth, NumerialHeight, numerials_32[first_num]);
   }
   
   dispCurrent->sendBuffer();
   delay(10000);

   dispCurrent->clearBuffer();
   dispCurrent->sendBuffer();
   delay(1000);

   resetDisplayX(display_current_number);
}

void showChangedSelection(String msg)
{
   //N:XX:XXX: (number changes on UI menu, selecting amount. Order is N:<price>:<volume>:)
   // 0 1 2 3 4 5 6 7 8
   // N : X X : X X X :
   Serial.println("Number change");
   Serial.print(msg);
   //Serial.print(msg[5]);

   uint8_t pn1,pn2,pn3;
   uint8_t vn1,vn2,vn3;
   
   uint8_t num_found_price = getDigitsFromString(msg,2,2,pn1,pn2,pn3);
   uint8_t num_found_vol = getDigitsFromString(msg,5,3,vn1,vn2,vn3);

   dispCurrent->clearBuffer();
   dispCurrent->drawXBMP(0, 0, takka_colon_width, takka_colon_height, takkaColon);

   //changed price
   if (num_found_price > 0)   dispCurrent->drawXBMP(takka_colon_width, 0, NumerialWidth, NumerialHeight, numerials_32[pn1]);
   if (num_found_price > 1)   dispCurrent->drawXBMP(takka_colon_width + NumerialWidth, 0, NumerialWidth, NumerialHeight, numerials_32[pn2]);
   
   //changed volume
   dispCurrent->drawXBMP(0,32,ML_width, ML_height, ML);
   if  (num_found_vol < 3){
      dispCurrent->drawXBMP(ML_width,32,NumerialWidth, NumerialHeight, numerials_32[vn1]);
      if  (num_found_vol == 2) dispCurrent->drawXBMP(ML_width+NumerialWidth,32,NumerialWidth, NumerialHeight, numerials_32[vn2]);
   }
   else{ //assume ==3
         dispCurrent->drawXBMP(ML_width,32,16, NumerialHeight, numerials_16[vn1]);
         dispCurrent->drawXBMP(ML_width+16,32,16, NumerialHeight, numerials_16[vn2]);
         dispCurrent->drawXBMP(ML_width+16+16,32,16, NumerialHeight, numerials_16[vn3]); // change
   }
   dispCurrent->sendBuffer();
}

void showProgress(String msg)
{
   //D:XX:XX: (dispensing progress updates. Order is D:<currentAmount>:<totalAmount>:)
   Serial.println("Progress");
   uint8_t num_found_1st_val, num_found_2nd_val;
   uint8_t v1_n1,v1_n2,v1_n3;
   uint8_t v2_n1,v2_n2,v2_n3;

   num_found_1st_val = getDigitsFromString(msg,2,2,v1_n1,v1_n2,v1_n3);
   num_found_2nd_val = getDigitsFromString(msg,5,2,v2_n1,v2_n2,v2_n3);

   dispCurrent->clearBuffer();
   dispCurrent->drawXBMP(16, 0, 96, 32, Dispensing);
   if (num_found_1st_val > 0) dispCurrent->drawXBMP(0, 32, 16, 32, numerials_16[v1_n1]);
   if (num_found_1st_val > 1) dispCurrent->drawXBMP(16, 32, 16, 32, numerials_16[v1_n2]);

   dispCurrent->drawXBMP(32, 32, 16, 32, div_bits);

   if (num_found_2nd_val == 1) dispCurrent->drawXBMP(48, 32, 16, 32, numerials_16[v2_n2]);
   if (num_found_2nd_val == 2){
      dispCurrent->drawXBMP(48, 32, 16, 32, numerials_16[v2_n2]);
      dispCurrent->drawXBMP(48 + 16, 32, 16, 32, numerials_16[v2_n2]);
   }

   dispCurrent->drawXBMP(48 + 32, 32, 48, 32, takka_bits);
   dispCurrent->sendBuffer();
    
}

void showPressGreen()
{
   dispCurrent->clearBuffer();
   dispCurrent->drawXBMP(0, 0, PressGreen_width, PressGreen_height, PressGreen);
   dispCurrent->sendBuffer();
}

void showPushBottle()
{
   dispCurrent->clearBuffer();
   dispCurrent->drawXBMP(0, 0, PushBottle_width, PushBottle_height, PushBottle);
   dispCurrent->sendBuffer();

}

void showCancel()
{
   dispCurrent->clearBuffer();
   dispCurrent->drawXBMP(0, 0, RedCancel_width, RedCancel_height, RedCancel);
   dispCurrent->sendBuffer();
}

void showPrinting()
{
   dispCurrent->clearBuffer();
   dispCurrent->drawXBMP(0, 0, 128, 64, Printing);
   dispCurrent->sendBuffer();
}

void showFinished()
{
   dispCurrent->clearBuffer();
   dispCurrent->sendBuffer();
   delay(1000);
   resetDisplayX(display_current_number);
}

uint8_t getDigitsFromString(String msg, uint8_t start_pos, uint8_t num_digits, uint8_t &val1, uint8_t &val2, uint8_t &val3)
{
  uint8_t digits_found = 0;
  val1 = val2 = val3 = 0;
  unsigned int msg_len = msg.length();

  for (uint8_t i = start_pos; i < msg_len && digits_found < num_digits; i++) {
    char c = msg[i];
    if (isdigit(c)) {
      uint8_t val = c - '0';
      switch (digits_found) { 
        case 0: val1 = val; break;
        case 1: val2 = val; break;
        case 2: val3 = val; break;
      }
      digits_found++;
    }
    else break;
  }

  return digits_found;
}

/* --- Arduino setup and loop Functions --- */
void setup(void)
{
   Serial.begin(115200);
   
   Wire.onReceive(onReceive);
   Wire.onRequest(onRequest);
   Wire.begin((uint8_t)I2C_DEV_ADDR); // Starting Wire as Slave

   for (size_t i = 0; i < NUM_DISPLAYS; i++)
   {
      dispArray[i]->begin();
      resetDisplayX(i);
   }
}

void loop(void)
{
}

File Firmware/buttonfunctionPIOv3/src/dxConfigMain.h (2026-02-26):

#ifndef DX_MAIN_H_FILE
#define DX_MAIN_H_FILE

#include <Arduino.h>

#define I2C_DEV_ADDR 0x55   //coms esp i2c address
#define DISPLAY_ADD 0x56    //display esp i2c address

#define BAUD_RATE 115200

// #define OPT_PRINT_LOGO

#define VERSION_BUTTONFUNCTIONPIO "3.4.0"


const uint32_t T_RAW_PERIOD = 30;       //period to send raw values of pins
const size_t NUM_PINS = 5;              //GPIO-buttons x4 and limits x1
const uint8_t NUM_BTNS = 4;             // used to specify the number of buttons per dispenser
const uint8_t NUM_DX = 4;               //number of dispensers
const uint8_t NUM_AMOUNTS = 3;          //number of amounts (preset volumes)

enum DxStates{
    STATE_IDLE = 0,
    STATE_ACTIVE,               // busy with selection of amount on specific dispenser
    STATE_WAIT_BTN_GREEN,       // wait for green ok
    STATE_WAIT_BEFORE_START,    // wait for period before going to wait for trigger
    STATE_WAIT_TRIGGER,         // wait for trigger before starting dispense
    STATE_DISPENSING,           // busy dispensing
    STATE_PRINTING,             // busy printing
    STATE_PAUSED,               // paused in dispense
    STATE_CANCEL,               // cancel dispense before dispense start
    STATE_CANCEL_IN_DX,         // cancel dispense after dispense start
    STATE_RAW_STREAM,           // print raw adc values for btn config
    STATE_MOTOR_TEST,           // run motors by cmd

    STATE_LOCKED,               // device locked, needs unlock 

};

// UI Button Order
enum BtnNumEnum{
    BTN_UP =   0,
    BTN_RED,
    BTN_DOWN,
    BTN_GREEN,
    BTN_NO_BTN = 99
};

//0: none, 1-4: DX, 5
enum MBtnEnum{
    BTN_EVENT_NA = 0,
    BTN_EVENT_DX1,
    BTN_EVENT_DX2,
    BTN_EVENT_DX3,
    BTN_EVENT_DX4,
    BTN_EVENT_LIM,
};

/*
=====================================================================
COMMANDS
=====================================================================
*/
enum ComCmds{
    //DISPENSER COMMANDS
    CMD_DX_ID = 0,                  // 0. print fw version number
    CMD_DX_SET_FEATURES,            // 1. set features; (bool has_printer, bool buzzer)

    //SET CONFIG
    CMD_CFG_FLOW_RATE = 20,         // 20. set ml/s; (flowrate_1,flowrate_2,flowrate_3,flowrate_4)
    CMD_CFG_RANGE_BTN_X,            // 21. set buttons voltages for btn X; (dx_num,low, high)
    CMD_CFG_RANGE_LIM_X,            // 22. set buttons voltages for lim X; (dx_num, low, high)
    CMD_CFG_PRODUCT_TABLE,          // 23. set product table for product; (dx_num, vol_1 (ml), price_1 (tk), vol_2 (ml), price_2 (tk), vol_3 (ml), price_3 (tk)) 

    CMD_CFG_GET_ALL,                // 24. get all cfg

    //do calibrate
    CMD_CAL_PRINT_RAW = 60,      // 66. enters/exits into raw stream mode (active: 1 / inactive: 0)
    // CMD_CAL_PRINT_DX = 60,  //   print dispenser voltage (dispenser number, number of readings to print)
    // CMD_CAL_PRINT_LIMS,     //   print limits  (number of readings to print)
    // CMD_CAL_DX,             //   auto cal btn voltage (dispenser number, number of readings)
    // CMD_CAL_LIM,            //   auto cal lims voltage ( number of readings)
    // CMD_CAL_PRINT_CURRENT,  //   print the current voltage ranges
    // CMD_CAL_PRINT_STREAM,   //   print stream data for plotting (dispenser number: 1-4, 5 limits, num points, sample period delay in ms)
    

    //printer interface
    CMD_PRINT_SIM_DX = 80,  // 80. simulate a dispense completed (int dispenserIndex, int amountDispensedTK, int enteredAmountTK)
    CMD_PRINT_SCAN_BT,      // 81. scan BT devices    
    CMD_PRINT_CONNECT,      // 82. try to connect to printer again  

    //motors
    CMD_MOTORS_RUNTIME = 100,   // 100. run motors for set time; (uint8 dx_num, uint16_t speed, bool fwd, uint32_t period) 
    CMD_MOTORS_STOP,            // 101. stop motors; ()

    //ESP or device 
    CMD_ESP_RESET = 120,    // 120. reset ESP
    CMD_ESP_UNLOCK,         // 121. unlock device; (char pwd)
    CMD_ESP_LOCK,           // 122. relock device; ()

  
};

/*
================================================================
serial com protocol
================================================================
*/

const char SERIAL_RX_END_CHAR = '\n'; //on what is received from host
const char SERIAL_RX_DELIM_CHAR = ','; //on what is receieved from host

static const size_t ARGS_CMDS_SIZE = 10; //max number of parameters for a command: <CMD_NUM>, param1, param2,... param_N
static const size_t ARGS_NUM_STRINGS = 3; //max number of strings, each with max length of SERIAL_NUM_RX_CHARS, <CMD_NUM>, string1..

//max length of a parameters/argument received, length of RX buffer per argument, also max len of string received by serial, max 2 strings
static const size_t SERIAL_NUM_RX_CHARS = 100; 


#define COM_PROTOCOL_DELIM "|" //separate com groups, <GROUP>|<NAME>|<msg>

//predefined keys
#define COM_KEY_MSG "MSG:"
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

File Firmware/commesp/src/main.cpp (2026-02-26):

#include <Arduino.h>
// Device configs
#include "commespcfg.h"
#include "pinmap.h"
// C99 libraries
// #include <cstdarg>
// #include <cstdlib>
// #include <string.h>
// #include <time.h>

// Libraries for MQTT client and WiFi connection
// #include <WiFi.h>
// #include <WiFiClientSecure.h>

// I2C
#include <Wire.h>
// Azure IoT SDK for C includes
// #include <az_core.h>
// #include <az_iot.h>


// Additional azure headers
// #include "AzureIoT.h"
// #include "Azure_IoT_PnP_Template.h"
// #include "iot_configs.h"

// serial RX
#include "serialparser.h"
// log util
#include "dxlogutil.h"
// wifi, mqtt and time
#include "dxclient.h"

SerialParser dxsp;
void _doCheckSerial();
int8_t _doParseCmd(ComCmds cmd, float *args);


// Timers



/* --- Settings from iot_configs.h --- */
// static const char* wifi_ssid = IOT_CONFIG_WIFI_SSID; 
// static const char* wifi_password = IOT_CONFIG_WIFI_PASSWORD;


// --- Function Declarations ---
void dxI2ConRequest();
void dxI2ConReceive();

// I2C
bool i2c_is_rdy = false;

void dxI2ConRequest() // Anwsers to Master's "requestFrom"
{
  // LogInfo("Request received. Sending buffered data."); //The sending happens on the background
}


// Anwsers to Master's "transmissions"
void dxI2ConReceive(int len) 
{
  // String response = "";  // request reply msg
  String rx_msg_str = "";   // to save Master's message
  // char rx_msg_chr[len] = "";
  // int msg_index = 0;

  // If there are bytes through I2C
  while (Wire.available())   rx_msg_str.concat((char)Wire.read()); // make a string out of the bytes

  // rx_msg_str.toCharArray(rx_msg_chr, len);  
  LogInfo("received message[%d]: %s", len,rx_msg_str.c_str());
  // Filter I2C Master messages
  // Ready: tell MainEsp if comms is ready, note this is not called by Main currently
  if (rx_msg_str == "Ready") 
  {
    String response_state = "Yes";
    // if (!send_device_info) product1String = "Yes";
    // else product1String = "No";
    
    int str_len = response_state.length() + 1;
    char char_array[str_len];
    response_state.toCharArray(char_array, str_len);
    Wire.slaveWrite((uint8_t *)char_array, str_len); // Adds the string to Slave buffer, sent on Request
  }
  // Main ESP request date, for printing on receipt
  else if(rx_msg_str=="Date")
  {
    String DT = getDateTime();
    int str_len = DT.length() + 1;
    char char_array[str_len];
    DT.toCharArray(char_array, str_len);
    Wire.slaveWrite((uint8_t *)char_array, str_len); 
  }
  // product messages, not used
  // must be dispense message
  else if(rx_msg_str[0]!='R' && rx_msg_str[0]!='P') 
  {
    sendMsgFormI2C(rx_msg_str); 
  }
}

/*
================================================================================================
MAIN SETUP AND LOOP
================================================================================================
*/
void setup()
{
  // Set serial monitor debugging window baud rate to 115200
  // Serial.begin(SERIAL_BAUD_RATE);
  dxsp.doStartup();
  set_logging_function(logging_function);

  // Start I2C communication
  Wire.onReceive(dxI2ConReceive);
  Wire.onRequest(dxI2ConRequest);
  Wire.begin((uint8_t)I2C_DEV_ADDR); // Starting Wire as Slave
  
  // start internet connection
  dxClientStartup();


  
}

void loop()
{
  _doCheckSerial();
  // dxWiFiProcessState();
  
  dxClientProcess();

}

void _doCheckSerial()
{
  //CHECK SERIAL
  if (dxsp.checkSerial())
  { 
      ComCmds cmd_num = dxsp.getCurrentCmd();
      float *data_ptr = dxsp.getRxDataPointer();
      int8_t cmd_error = _doParseCmd(cmd_num,data_ptr);
      dxsp.clear(cmd_error);

  }
}

int8_t _doParseCmd(ComCmds cmd, float *args)
{
  int8_t error_code = 0;
  float value_1 = args[0];
  // float value_2 = args[1];
  // float value_3 = args[2];
  // float value_4 = args[3];
  char (*cfg_strings)[SERIAL_NUM_RX_CHARS] = dxsp.getStringValues();

  switch (cmd){
    case CMD_DX_ID:
      LogInfo(COM_DX_MSG "version:%s",VERSION_COMMESP);
      break;

    //==================================
  
    //==================================
    //ESP CMDS
    case CMD_ESP_RESET:
      LogInfo("DO ESP RESTART...");
      delay(500);
      esp_restart();
      break;

    //==================================
    case CMD_MQTT_GET_STATE:
      dxClientPrintState();
      break;

    case CMD_MQTT_GET_WIFI_CRED:
      dxWifiPrintCred();
      break;
    
    case CMD_MQTT_GET_DEV_ID:
      dxClientGetDevNum();
      break;

    case CMD_MQTT_GET_DATE:
      LogInfo(COM_DX_MSG "date:%s",getDateTime().c_str());
      break;

    case CMD_MQTT_SET_WIFI_CRED:
      dxWifiSetCred(cfg_strings[0],cfg_strings[1]);
      break;

    case CMD_MQTT_SET_DEV_ID:
      dxClientSetDevNum((uint32_t) value_1);
      break;

    case CMD_MQTT_SIM_DX:
      if (value_1 == 1) dxClientSimDx();
      break;

    case CMD_MQTT_FORCE_RESTART:
    if (value_1 == 1) dxClientRestart();
    break;

    default:
      error_code = -1;
      break;
  };

  return error_code;
}

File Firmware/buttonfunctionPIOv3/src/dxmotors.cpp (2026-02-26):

#include "dxmotors.h"


void DxMotors::_stopIfDirChange(bool fwd)
{
  if (isRunning() && !isDirection(fwd)) stop();
}

void DxMotors::_stopIfDiffDx(uint8_t dx_index)
{
  if (isRunning() && dx_index != _dx_num) stop();
}

void DxMotors::doInit()
{
  /* --- PWM Properties --- */
  const int freq = 30000;
  const int pwmChannel1 = 0;
  const int pwmChannel2 = 1;
  const int pwmChannel3 = 2;
  const int pwmChannel4 = 3;
  const int resolution = 8;

  pinMode(DX_PIN_M1_P1, OUTPUT);
  pinMode(DX_PIN_M1_P2, OUTPUT);
  
  pinMode(DX_PIN_EN_M1, OUTPUT);
  pinMode(DX_PIN_EN_M2, OUTPUT);
  pinMode(DX_PIN_EN_M3, OUTPUT);
  pinMode(DX_PIN_EN_M4, OUTPUT);

  // configure LED PWM functionalitites
  ledcSetup(pwmChannel1, freq, resolution);
  ledcSetup(pwmChannel2, freq, resolution);
  ledcSetup(pwmChannel3, freq, resolution);
  ledcSetup(pwmChannel4, freq, resolution);
  
  // attach the channel to the GPIO to be controlled
  ledcAttachPin(DX_PIN_EN_M1, pwmChannel1);
  ledcAttachPin(DX_PIN_EN_M2, pwmChannel2);
  ledcAttachPin(DX_PIN_EN_M3, pwmChannel3);
  ledcAttachPin(DX_PIN_EN_M4, pwmChannel4);

  stop();
}

void DxMotors::stop()
{
  analogWrite(DX_PIN_EN_M1, 0);
  analogWrite(DX_PIN_EN_M2, 0);
  analogWrite(DX_PIN_EN_M3, 0);
  analogWrite(DX_PIN_EN_M4, 0);

  digitalWrite(DX_PIN_M1_P1, LOW);
  digitalWrite(DX_PIN_M1_P2, LOW);

  if (_is_running) Serial.println(COM_MOTORS_MSG COM_KEY_MSG "stopped");
  _is_running = false;
}

void DxMotors::run(uint8_t dx_index,uint16_t speed,bool fwd)
{
  dx_index = constrain(dx_index,1,4);
  _stopIfDirChange(fwd);
  _stopIfDiffDx(dx_index);

  speed = constrain(speed,0,255);
  uint8_t pin = _en_pins[dx_index  -1];
  Serial.printf(COM_MOTORS_MSG COM_KEY_MSG "run,dx:%u,speed:%u,dir:%d\n",dx_index,speed,fwd);
  analogWrite(pin, speed);

  if (fwd){
      digitalWrite(DX_PIN_M1_P1, HIGH);
      digitalWrite(DX_PIN_M1_P2, LOW);
  }
  else{
      digitalWrite(DX_PIN_M1_P1, LOW);
      digitalWrite(DX_PIN_M1_P2, HIGH);
  }
  _fwd = fwd;
  _is_running = true;
  _dx_num = dx_index;
}

void DxMotors::startRunForTimePeriod(uint8_t dx_index, uint16_t speed, bool fwd, uint32_t period)
{
  
  _time_period = period;
  _time_start = millis();
  Serial.printf(COM_MOTORS_MSG COM_KEY_MSG "run for period, period: %u\n",period);
  run(dx_index,speed,fwd); //will stop motor if different direction or dx_num
}

void DxMotors::doRunForPeriod(uint32_t time_stamp)
{
  uint16_t print_max = 500;
  static uint16_t print_cnt = print_max;
  if (_time_start >= time_stamp) return; //should not get here...
  if (_time_period == 0) return; //0 time period -- run infinitely
  if (!_is_running) return; //stopped already

  float progress = 100;
  uint32_t time_done = time_stamp - _time_start;
  //check if time to stop
  if (time_done >= _time_period)
  {
    stop();
    print_cnt = print_max;
  }
  //else update progress % 
  else progress = 100.0*time_done/_time_period;
  //report progress
  if (print_cnt++ >= print_max)
  {
    Serial.printf(COM_MOTORS_MSG "pro:%.2f\n",progress);
    print_cnt = 0;
  }
}

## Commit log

2026-02-26 add QA tool "buttonApp"
2026-03-31 Rename Dispenser Final BOM.xlsx to Dispenser Final BOM.xlsx
    [Dispenser Final BOM.xlsx]
